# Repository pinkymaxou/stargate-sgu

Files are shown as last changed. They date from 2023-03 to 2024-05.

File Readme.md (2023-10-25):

**Warning**: This project contains several hundred parts to print and hundreds hours of print.
If you decide to take this path you will suffer a lot, you may lose some compatriot in the battle.
You will no longer be the same after that, it could also cause hair loss.

# Stargate Universe

This project is basically a small stargate made to decorate your desk. It features lightning for symbols like in the serie and the ring spins.

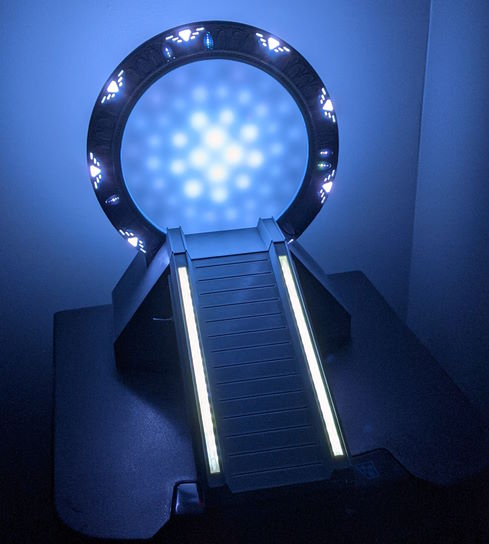
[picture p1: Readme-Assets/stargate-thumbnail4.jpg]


https://www.youtube.com/watch?v=xp08K564FYA for more details.

Unfortunately this project went through a lot of trial and error, so there are more parts than it should have especially in the base.
Optimize it would require making a second gate to test new optimization.
I'm no willing to do that now.

Inspired partly by:

| URL |
|---|
| https://thestargateproject.com/build-a-stargate-and-dhd-3d-printed/ |
| https://www.youtube.com/watch?v=m0cj_5DWYjw&ab_channel=StargateFan |

# Knowns issues

- The start-up and recharge plunger is not perfect, using pogo pin and gold plated female contactor may improve it.

# Copyrights & Thanks

Copyright:
|File | Info
|---|---
| stargateuniverse.woff | Created by : Gilles Nuytens (http://www.thescifiworld.net/fonts.htm)
| eurostile_extended2_bold.woff | https://fontsgeek.com/fonts/eurostile-extended-2-bold?ref=readme
| ancient_virtual.ttf.woff | Created by VirtualCLD (http://www.thescifiworld.net/fonts.htm)
| MGM (for the franchise)
| Explanation and inspiration for the design | https://stargate.fandom.com/wiki/Glyph#Milky_Way_glyphs
| Adafruit | OLED library |

|File | Info
|---|---
| DF Robot | https://www.dfrobot.com/
| Embedded file generator (python) | Created by ducalex https://github.com/ducalex

# Original gate

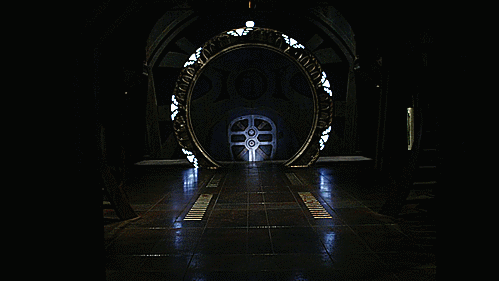
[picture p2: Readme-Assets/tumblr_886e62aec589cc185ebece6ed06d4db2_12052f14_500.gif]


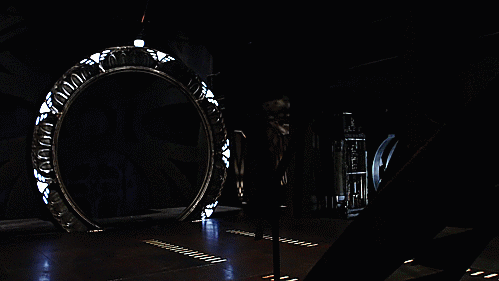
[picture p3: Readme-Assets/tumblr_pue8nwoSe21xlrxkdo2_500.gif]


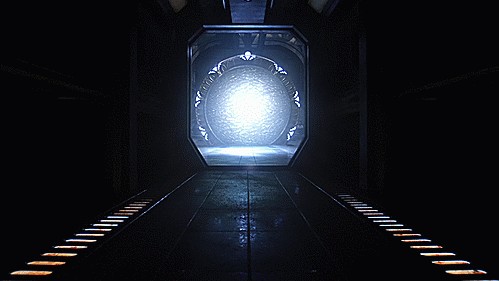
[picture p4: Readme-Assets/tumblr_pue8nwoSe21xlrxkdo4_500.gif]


# Prerequisites

 - Correct knowledge of ESP32 and programming with ESP-IDF
 - At least 22 x 22 cm printer, capable of printing with 0.2 mm nozzle (yes, 0.2mm !)<br>
    **Warning: Don't even think of printing it using a bigger nozzle, it just won't work.**
 - Have some knowledge in electronic.
 - ESP-IDF toolkit installed (tested on IDF 5.0)

# Included softwares

| Name | Description |
|---|---|
| base-fw | Base control firmware |
| ring-factory | Basic firmware to upload firmware into ring |
| ring-fw | Ring firmware |
| tools/otauploader.py | Do upload using HTTP for OTA |
| tools/embeddedgen.py | Generate embedded resources |

# Electronic board

A new electronic board has been created. Not yet tested entierely.

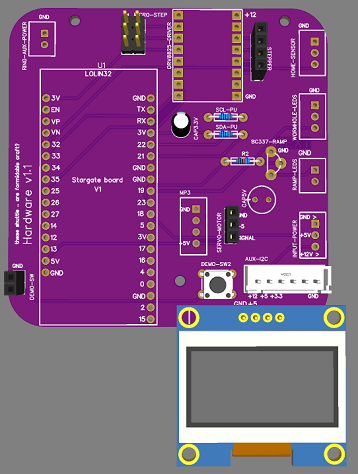
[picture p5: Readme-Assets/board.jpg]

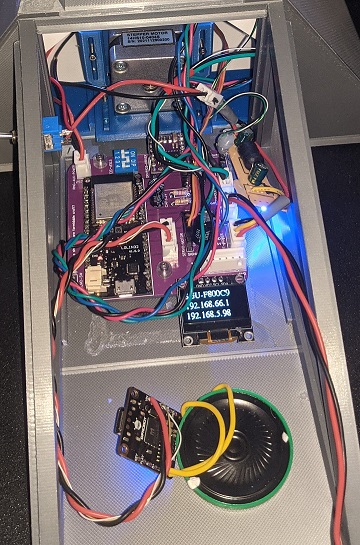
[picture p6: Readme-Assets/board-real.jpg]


# Parts to print

##  Ring

| File name | Count |
|---|---|
| Alignment-block-0.2mm_x9.stl | 9
| Chevron-insert-tool.stl | 1
| Home-magnet-holder_0.4mm-x1.stl | 1
| Inner-ring-0.4mm_x1.stl | 1
| Inner-ring-sensor-holder_0.4mm-x1.stl | 1
| Light-chevron-0.2mm_x18.stl | 18
| Light-chevron-cover-0.2mm-x9.stl | 9
| Magnet-ring-0.2mm-x1.stl | 1
| Module-With_wheel-0.2mm_x18.stl | 18
| Stargate-Back-0.2mm_x1.stl | 1
| Stargate-Back-Transparent-PwrSw_0.2mm-x1 | 1
| Stargate-Back-Transparent-ResetBtn_0.2mm-x1 | 1
| Stargate-Back-TransWindow-0.2mm-x10-12.stl | 12
| Stargate-Front-0.2mm_x1.stl | 1
| Symbols/symbol-template10_0.2mm-x1.stl | 1
| Symbols/symbol-template11_0.2mm-x1.stl | 1
| Symbols/symbol-template12_0.2mm-x1.stl | 1
| Symbols/symbol-template13_0.2mm-x1.stl | 1
| Symbols/symbol-template14_0.2mm-x1.stl | 1
| Symbols/symbol-template15_0.2mm-x1.stl | 1
| Symbols/symbol-template16_0.2mm-x1.stl | 1
| Symbols/symbol-template17_0.2mm-x1.stl | 1
| Symbols/symbol-template18_0.2mm-x1.stl | 1
| Symbols/symbol-template19_0.2mm-x1.stl | 1
| Symbols/symbol-template1_0.2mm-x1.stl | 1
| Symbols/symbol-template20_0.2mm-x1.stl | 1
| Symbols/symbol-template21_0.2mm-x1.stl | 1
| Symbols/symbol-template22_0.2mm-x1.stl | 1
| Symbols/symbol-template23_0.2mm-x1.stl | 1
| Symbols/symbol-template24_0.2mm-x1.stl | 1
| Symbols/symbol-template25_0.2mm-x1.stl | 1
| Symbols/symbol-template26_0.2mm-x1.stl | 1
| Symbols/symbol-template27_0.2mm-x1.stl | 1
| Symbols/symbol-template28_0.2mm-x1.stl | 1
| Symbols/symbol-template29_0.2mm-x1.stl | 1
| Symbols/symbol-template2_0.2mm-x1.stl | 1
| Symbols/symbol-template30_0.2mm-x1.stl | 1
| Symbols/symbol-template31_0.2mm-x1.stl | 1
| Symbols/symbol-template32_0.2mm-x1.stl | 1
| Symbols/symbol-template33_0.2mm-x1.stl | 1
| Symbols/symbol-template34_0.2mm-x1.stl | 1
| Symbols/symbol-template35_0.2mm-x1.stl | 1
| Symbols/symbol-template36_0.2mm-x1.stl | 1
| Symbols/symbol-template3_0.2mm-x1.stl | 1
| Symbols/symbol-template4_0.2mm-x1.stl | 1
| Symbols/symbol-template5_0.2mm-x1.stl | 1
| Symbols/symbol-template6_0.2mm-x1.stl | 1
| Symbols/symbol-template7_0.2mm-x1.stl | 1
| Symbols/symbol-template8_0.2mm-x1.stl | 1
| Symbols/symbol-template9_0.2mm-x1.stl | 1
| symbol-light-guide_0.2mm-x36.stl | 36
| Lower-bridge-0.4mm-x1.stl | 1
| TOTAL | 148

## Base

| File name | Count |
|---|---|
| Back-plunger-anchor_4mm-x2.stl | 2
| Back-plunger-arm_4mm-x1.stl | 1
| Back-plunger-bar_4mm-x1.stl | 1
| Back-plunger-Higher-spring_4mm-x1.stl | 1
| Back-plunger-Lower-spring_4mm-x1.stl | 1
| black-plunger-hammer-cover_4mm-x1.stl | 1
| black-plunger-hammer_4mm-x1.stl | 1
| Board-holder_4mm-x1.stl | 1
| Bottom-plate-v2_4mm-x1.stl | 1
| magnet-gear_4mm-x1.stl | 1
| Mechanic-Anchor-L_4mm-x1.stl |1
| Mechanic-Anchor-R_4mm-x1.stl | 1
| Mechanic-Archor-p2-L_4mm-x1.stl | 1
| Mechanic-Archor-p2-R_4mm-x1.stl | 1
| Outer-back-cover-plug-blocking_4mm-x1.stl | 1
| Outer-back-cover-plug_4mm-x1.stl | 1
| Outer-back-cover_4mm-x1.stl | 1
| Outer-back-plate-reinforcement_4mm-x1.stl | 1
| Outer-back-plate_4mm-x1.stl | 1
| Outer-bottom-plate2_4mm-x1.stl | 1
| Outer-bottom-plate_4mm-x1.stl | 1
| Outer-front-plate_4mm-x1.stl | 1
| Outer-side-plate#1_4mm-x1.stl | 1
| Outer-side-plate#2_4mm-x1.stl | 1
| ramp-light-guide_4mm-x2.stl | 2
| Ramp_4mm-x1.stl | 1
| Side-back-cover-L_4mm-x1.stl | 1
| Side-back-cover-R_4mm-x1.stl | 1
| Side-ramp-cover-L_4mm-x1.stl | 1
| Side-ramp-cover-R_4mm-x1.stl | 1
| spacer_4mm-x4.stl | 4
| Stepper-bracket_4mm-x1.stl | 1
| Stepper-mount-1_4mm-x1.stl | 1
| Stepper-mount-2_4mm-x1.stl | 1
| top-cover_4mm-x1.stl | 1
| Truss#1_4mm-x1.stl | 1
| Truss#2_4mm-x1.stl | 1
| Side-overcover-L_4mm-x1.stl | 1
| Side-overcover-R_4mm-x1.stl | 1
| TOTAL | 44

## Wormhole

| File name | Count |
|---|---|
| Wormhole.stl | 1
| Wormhole-outer-rim.stl | 1
| Wormhole-filter.stl | 1
| TOTAL | 3

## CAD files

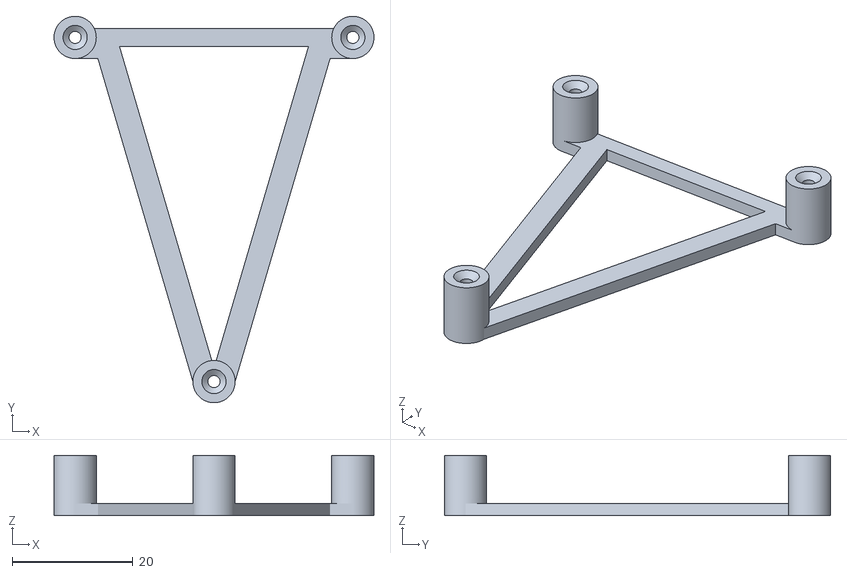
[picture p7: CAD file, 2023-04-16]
Build-Instructions/Base/Board-holder_4mm-x1.stl
53.0 x 64.0 x 10.0

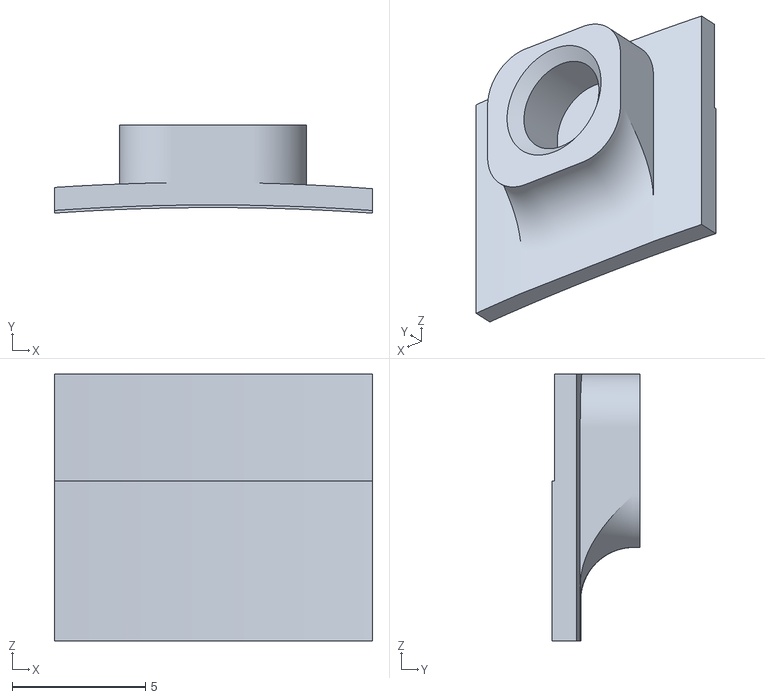
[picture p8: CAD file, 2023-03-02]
Build-Instructions/Ring/Home-magnet-holder_0.4mm-x1.stl
11.9 x 3.32 x 10.0

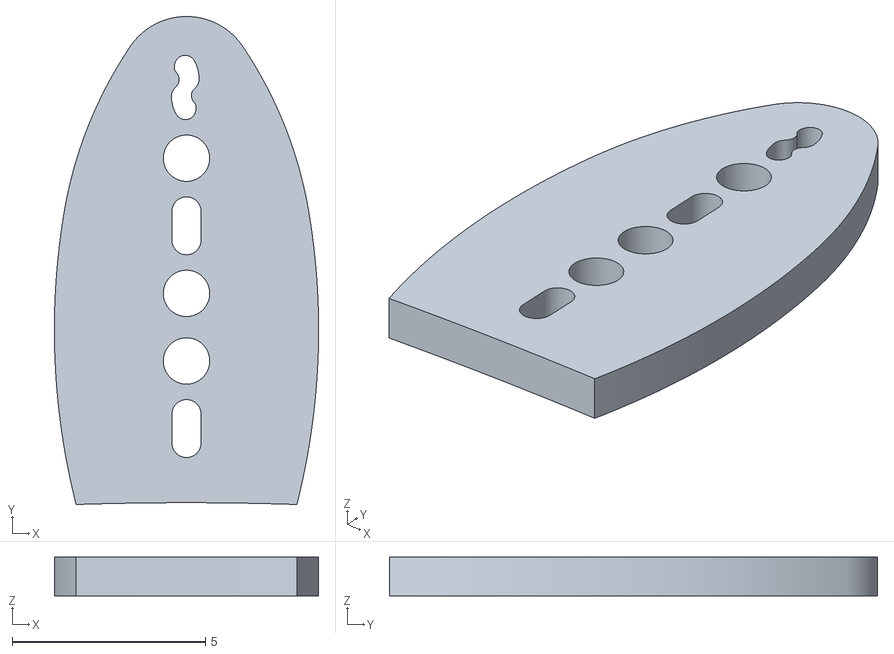
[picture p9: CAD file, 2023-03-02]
Build-Instructions/Ring/Symbols/symbol-template1_0.2mm-x1.stl
6.84 x 12.6 x 1.00

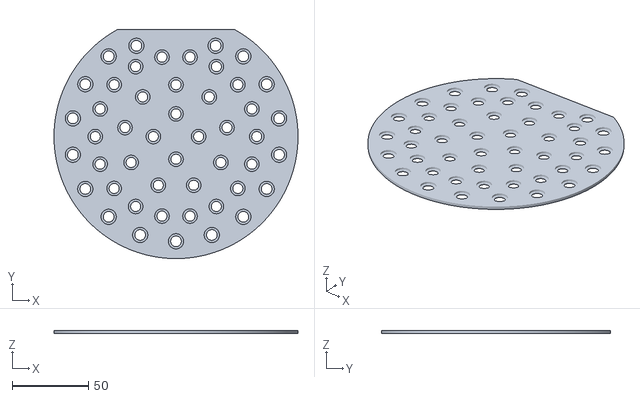
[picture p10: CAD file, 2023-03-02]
Build-Instructions/Wormhole/Wormhole.stl
160.2 x 150.4 x 2.00

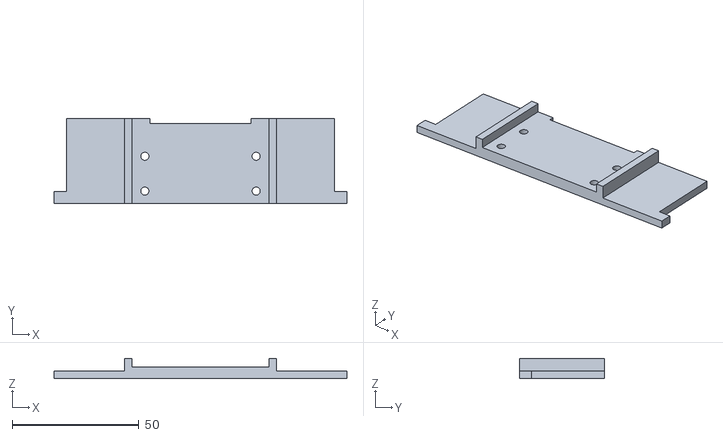
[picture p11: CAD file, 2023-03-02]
Build-Instructions/Base/Stepper-mount-1_4mm-x1.stl
115.8 x 33.8 x 8.00

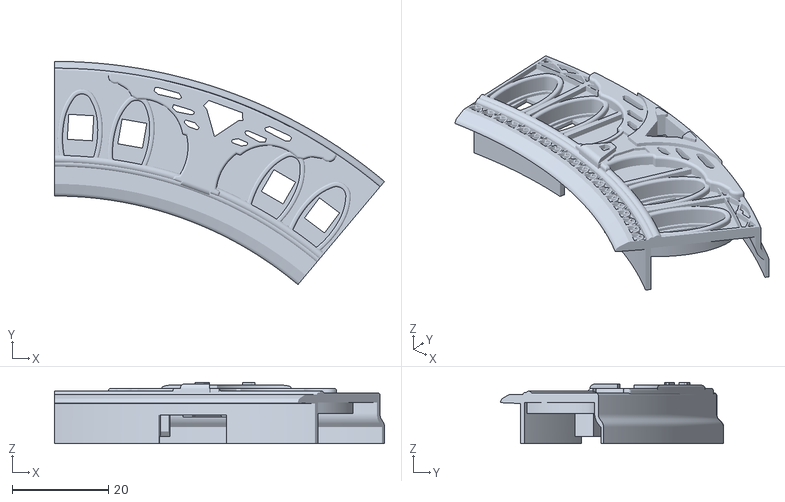
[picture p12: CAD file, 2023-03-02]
Build-Instructions/Ring/TestPart-Stargate-Front.stl
68.4 x 46.3 x 12.7

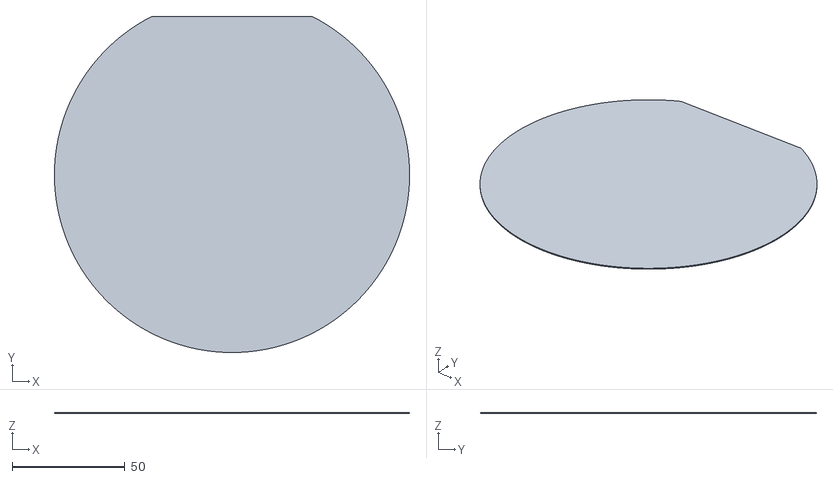
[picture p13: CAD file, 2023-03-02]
Build-Instructions/Wormhole/Wormhole-filter.stl
157.5 x 149.0 x 0.5

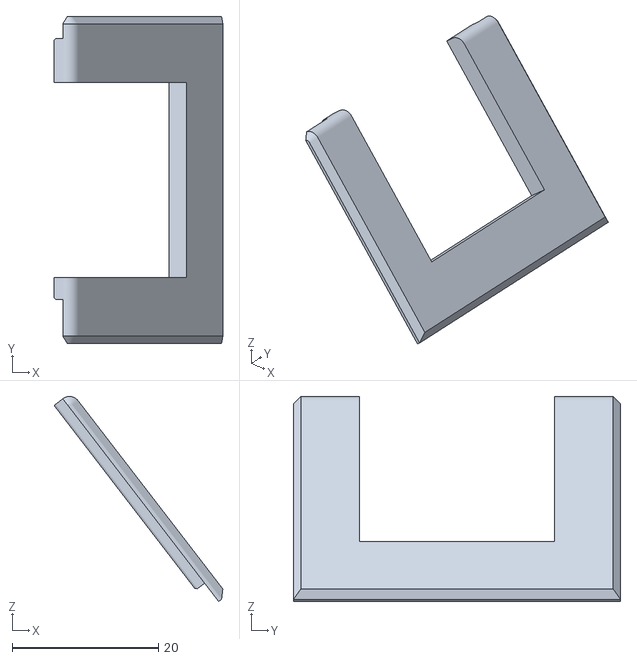
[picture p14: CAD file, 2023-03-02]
Build-Instructions/Base/Side-overcover-R_4mm-x1.stl
23.1 x 44.7 x 28.0

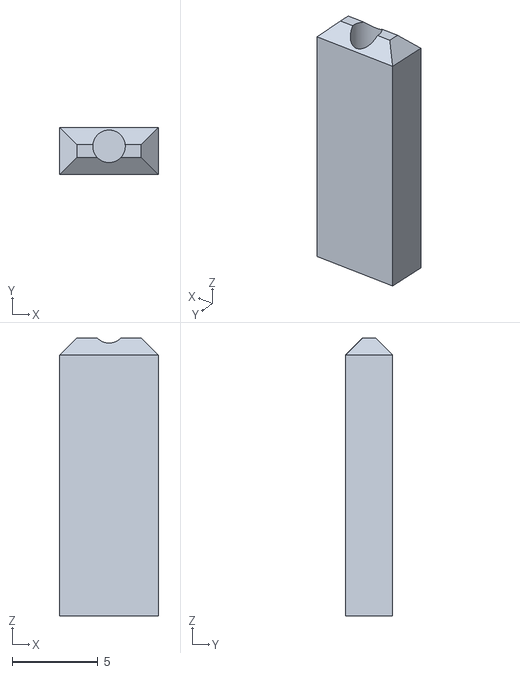
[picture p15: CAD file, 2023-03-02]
Build-Instructions/Ring/Alignment-block-0.2mm_x9.stl
5.76 x 2.76 x 16.2

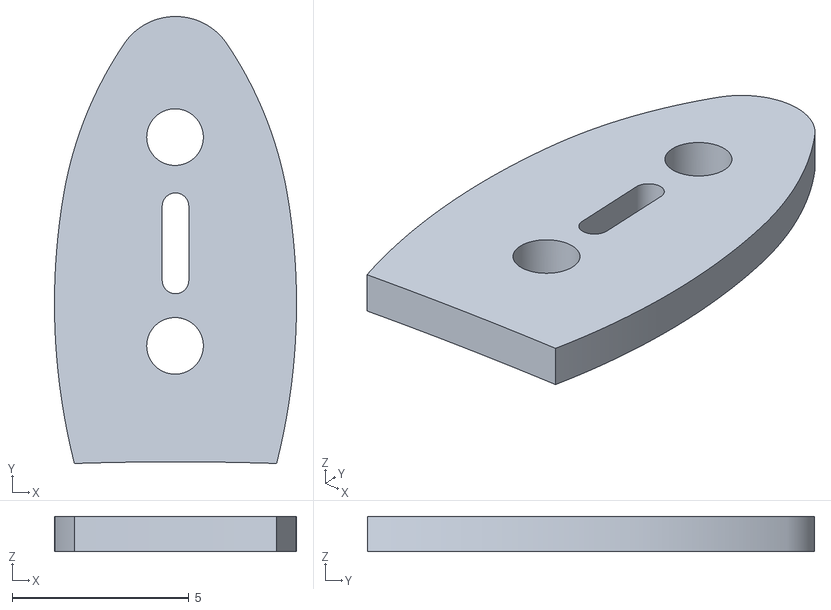
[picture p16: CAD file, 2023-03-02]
Build-Instructions/Ring/Symbols/symbol-template34_0.2mm-x1.stl
6.84 x 12.6 x 1.00

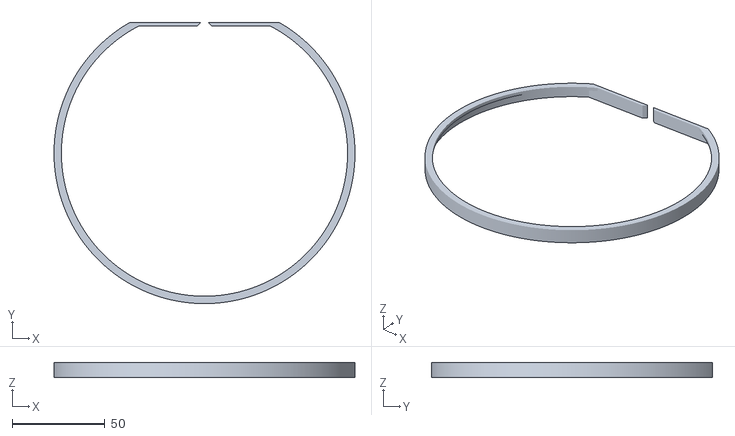
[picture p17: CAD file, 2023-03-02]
Build-Instructions/Wormhole/Wormhole-outer-rim.stl
162.0 x 151.3 x 8.00

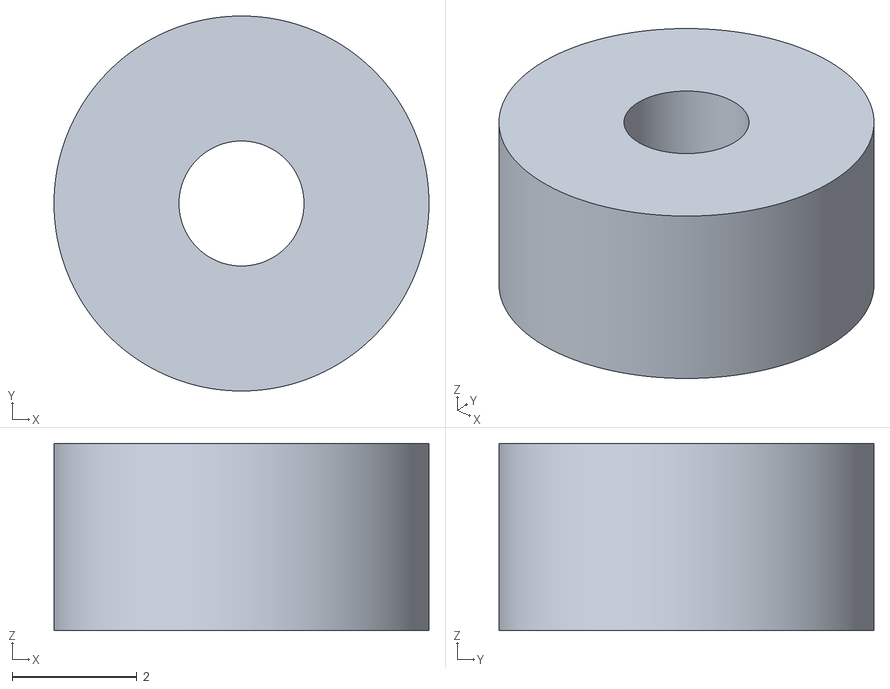
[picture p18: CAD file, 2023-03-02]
Build-Instructions/Base/spacer_4mm-x4.stl
6.00 x 6.00 x 3.00

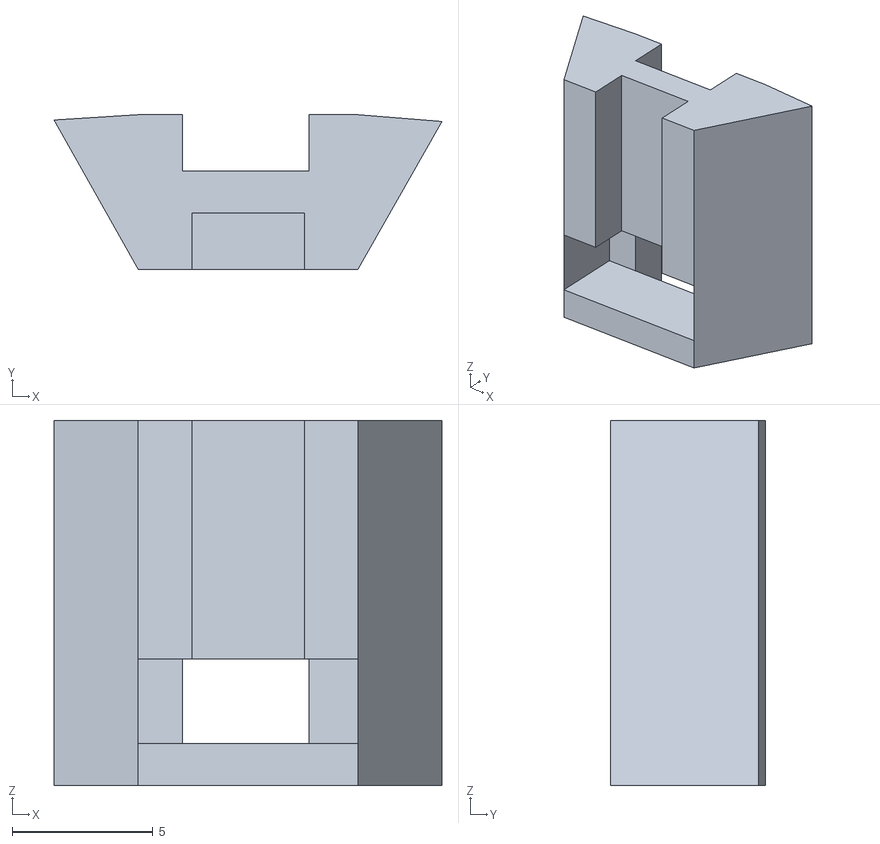
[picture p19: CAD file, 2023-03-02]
Build-Instructions/Ring/Inner-ring-sensor-holder_0.4mm-x1.stl
13.8 x 5.50 x 13.0

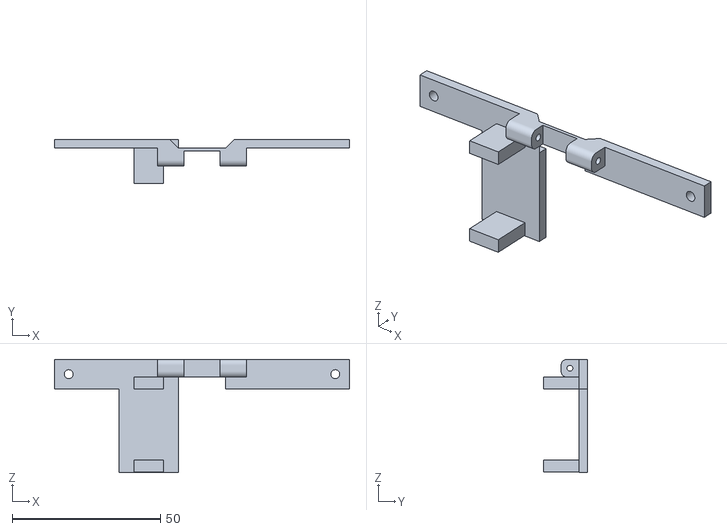
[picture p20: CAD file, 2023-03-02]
Build-Instructions/Base/Back-plunger-bar_4mm-x1.stl
99.6 x 15.0 x 38.3

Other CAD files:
Build-Instructions/Ring/Symbols/symbol-template18_0.2mm-x1.stl
Build-Instructions/Ring/Symbols/symbol-template3_0.2mm-x1.stl
Build-Instructions/Ring/Magnet-ring-0.2mm-x1.stl
Build-Instructions/Ring/Symbols/symbol-template16_0.2mm-x1.stl
Build-Instructions/Base/Back-plunger-Higher-spring_4mm-x1.stl
Build-Instructions/Base/Back-plunger-Lower-spring_4mm-x1.stl
Build-Instructions/Base/Back-plunger-anchor_4mm-x2.stl
Build-Instructions/Base/Back-plunger-arm_4mm-x1.stl
Build-Instructions/Base/Bottom-plate-v2_4mm-x1.stl
Build-Instructions/Base/Mechanic-Anchor-L_4mm-x1.stl
Build-Instructions/Base/Mechanic-Anchor-R_4mm-x1.stl
Build-Instructions/Base/Mechanic-Archor-p2-L_4mm-x1.stl
Build-Instructions/Base/Mechanic-Archor-p2-R_4mm-x1.stl
Build-Instructions/Base/Outer-back-cover-plug-blocking_4mm-x1.stl
Build-Instructions/Base/Outer-back-cover-plug_4mm-x1.stl
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

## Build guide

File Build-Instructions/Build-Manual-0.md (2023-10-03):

# Material prerequisite

## Electronics

| Description | Quantity | URL
|---|---|---|
| MOSFET P Channel | 1 | https://www.aliexpress.com/item/32884055864.html |
| NPN Transistor (BC337) | 1 |  |
| LEDs WS2812B | 100 | https://www.aliexpress.com/item/1005002657432751.html |
| 693ZZ bearings (8mm wide, 4mm thick, 3mm inner)  | 9 |  https://www.aliexpress.com/item/557757520.html |
| M5Stack Official M5Stamp Pico | 1 |  https://www.aliexpress.com/item/1005003449579749.html |
| LiPo Charger with 5v boost | | https://www.aliexpress.com/item/4000935870120.html |
| LiPo battery | 4x 100mA  | https://www.aliexpress.com/item/32853990764.html (any will do as long as it fit into the ring) |
| ESP32, example: Lolin32 | 1 | Any with enough output pin will do. |
| Fermion DFPlayer Pro Mini MP3 | 1 | https://www.aliexpress.com/item/4000394488862.html |
| DRV8825 Stepper Motor Controller | 1 | https://www.amazon.ca/-/fr/DRV8825-remplacement-TMC2208-Dissipateur-thermique/dp/B095LRJR2S |
| Resistors kit | |
| Capacitor kit | |
| A few schottky diodes | |
| All kind of wires | (24 to 26 AWG mostly) |
| 12 volts to 5 volts step converter (2A) | 1 | https://www.aliexpress.com/item/1005001534795169.html
| 12 mm tactile switch | 1 |
| Hall-Effect Sensor Digital 3144 | 1 | https://www.aliexpress.com/item/32823025060.html (Any will do as long as it's digital)
| JST Connecteur Kit 2.54 mm | 1 | https://www.amazon.ca/Bestgle-Connector-JST-XHP-Housing-Adapter/dp/B07MBCLPBK/ref=asc_df_B07MBCLPBK/

## Mechnical parts

| Description | Quantity | URL |Comments
|---|---|---|---|
| NEMA 14 stepper | 1 | https://www.amazon.ca/0-9deg-steps-Precision-Stepper-15-6oz/dp/B00PNEPZQC
| 4x2 mm magnets  | 160 | https://www.aliexpress.com/item/1005002591601630.html |
| Privacy film  | 25x25 cm at least | https://www.aliexpress.com/item/32967449727.html |
| Copper tape  | 1 | https://www.aliexpress.com/item/1005002822966859.html |
| Plexiglass 20x20cm (recommend buying spare)  | 1 + 1 spare | https://www.aliexpress.com/item/32833660352.html |
| Servo 9g | 1 | https://www.amazon.ca/-/fr/Servo-num%C3%A9rique-Micro-Metal-mod%C3%A8le/dp/B07FPJYM5T | We tried cheap one but they proved to be problematic, one died suddently and the other draw too much current sometime. You may have to invest in something better.
| M2 screws kit | 1 | https://www.amazon.ca/-/fr/Hilitchi-Assortiment-hexagonale-acier-inoxydable/dp/B014ONS02S | You needs several lengths
| M3 screws kit | 1 | https://www.amazon.ca/Assortiment-cruciformes-cylindrique-acier-inoxydable/dp/B075RCVVYN/ | You needs several lengths

## 3D Printing parts

| Description | Quantity | URL
|---|---|---|
| Nozzle 0.2mm | 1 | Required to get nice results

## Recommendations

Parts are printed at very high resolution (by FDM standard) and printing require for several days in some case. It's very important to have a good way to ensure it sticks in place.

| Description | Quantity | URL
|---|---|---|
| Dremel Purple Glue | 1 | https://www.amazon.ca/Dremel-GS45-01-Glue-Sticks/dp/B077FVQ3DX
| Magigoo | 1 | https://shop3d.ca/products/magigoo-3d-printing-adhesive-50ml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

## MISC

| Description | Quantity | Description
|---|---|---|
| Gorilla Super Glue | 1 | Used to glue the most important parts.
| Canopy Glue | 1 | Need a glue that turn transparent. Gorilla glue stain the plexiglass and leave horrible traces.
| Hot Glue | 1 | It could be done with canopy glue too but it's easier to remove hot glue if necessary.
| Small clamps to hold parts while curing | 1 |

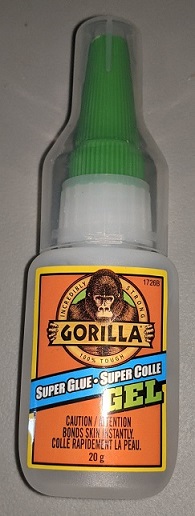
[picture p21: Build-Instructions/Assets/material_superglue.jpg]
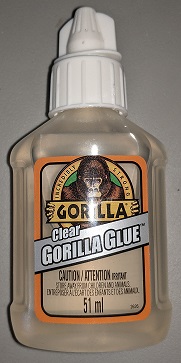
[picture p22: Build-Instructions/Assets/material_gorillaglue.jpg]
  

## Required plastics

Basically color is up to you, but you will probably needs at least 3 colors.<br>
Nothing prevent you from painting parts if you can't find the right plastic color. If you do it, we suggest using dark PLA before painting over the ring, to be sure lights do not leak.

| Color | Used for | Comments
|---|---|---|
| Dark gray or black PLA | Ring | The ring in the serie is almost black if not black. The one we made was gray but not dark enough, if we could do it again we would likely make it black |
| Transparent PLA | Ring | Used for chevron illumination and light diffusion. It may be possible to use white instead but we suggest you to test it before commiting yourself.
| White PLA | Ring/Base | Used for reflectors but can be used for any parts that is not visible. (example, bearing module, inner ring, alignment block etc ...)
| Sand PLA | Base | Sand like color, yes we realise there are many possible color for sand so let's say the same color as pyramid of egypt?

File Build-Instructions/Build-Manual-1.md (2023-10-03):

# Recommendation

## Before printing

We provide "TestPart-Stargate-Front.stl" part to test printing 1/9 of the front stargate part.<br>
It allows you to test material or print settings before doing the big part.

We recommend you to print these parts using the color or plastic of your choice :

- TestPart-Stargate-Front.stl
- Light-chevron-0.2mm_x18.stl
- symbol-light-guide_0.2mm-x36.stl
- symbol-template1_0.2mm-x1.stl

It is better if you also have one WS2812B to test the chevron and symbol lightning.<br>
The LED shouldn't be at full power to test symbols, only 5/255 PWM is enough to see it clearly.<br>
It could be higher for chevron but your don't gain anything going beyond 160/255 except excessive power loss.<br>

If you want to use a resin printer for symbols you can, but you will likely have to paint them because resin transparency is not adequate in our experience.

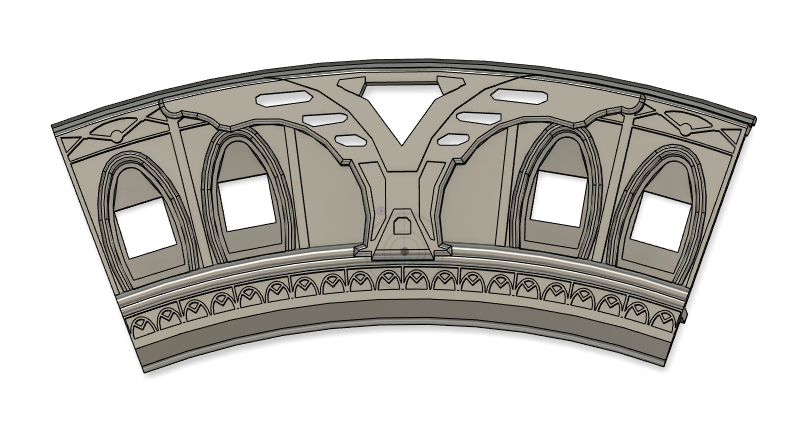
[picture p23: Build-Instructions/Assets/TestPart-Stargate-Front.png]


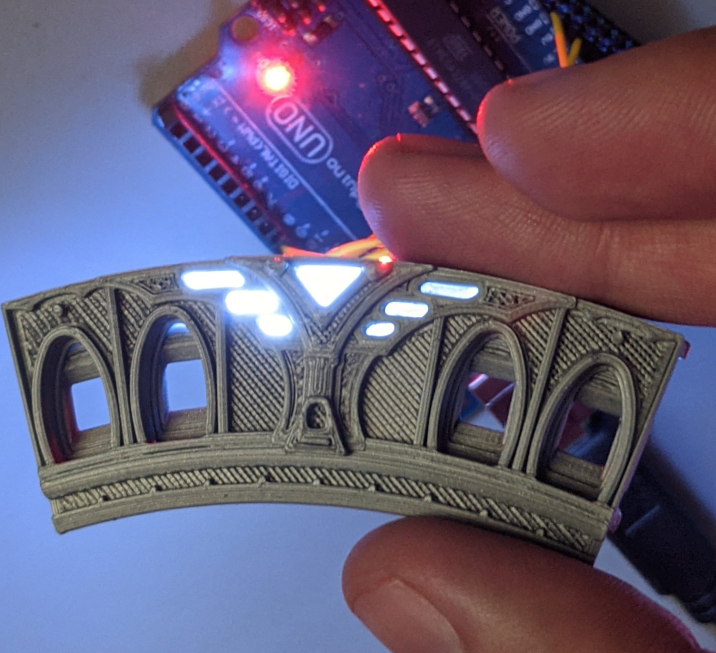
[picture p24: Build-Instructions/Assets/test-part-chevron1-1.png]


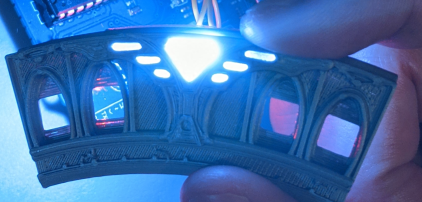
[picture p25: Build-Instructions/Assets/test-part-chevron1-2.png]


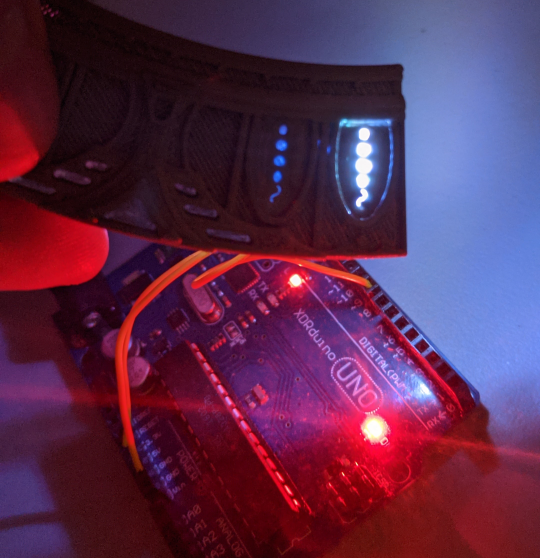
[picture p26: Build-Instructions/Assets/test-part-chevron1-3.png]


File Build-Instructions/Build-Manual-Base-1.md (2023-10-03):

# Base assembly

Don't worry about the ringmotor assembly, it could be inserted later.<br>
It is designed to be easy to disassemble.

 - You need a lot of small clamp if you want to do a decent job. we have found them at dollar store and they worth every penny.
 - Gorilla glue or canopy glue

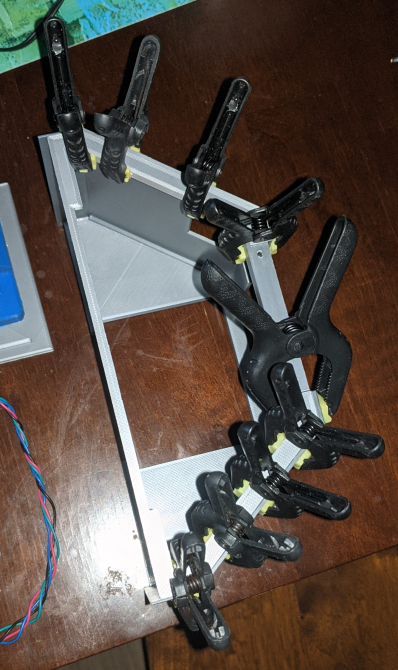
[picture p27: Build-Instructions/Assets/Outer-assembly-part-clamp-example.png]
 

## Glue base parts #1

Glue all those parts together, use the picture to guide you.<br>
You needs those part to continue:

 - Outer-bottom-plate_4mm-x1.stl
 - Outer-bottom-plate2_4mm-x1.stl
 - Outer-front-plate_4mm-x1.stl
 - Outer-side-plate#1_4mm-x1.stl
 - Outer-side-plate#2_4mm-x1.stl

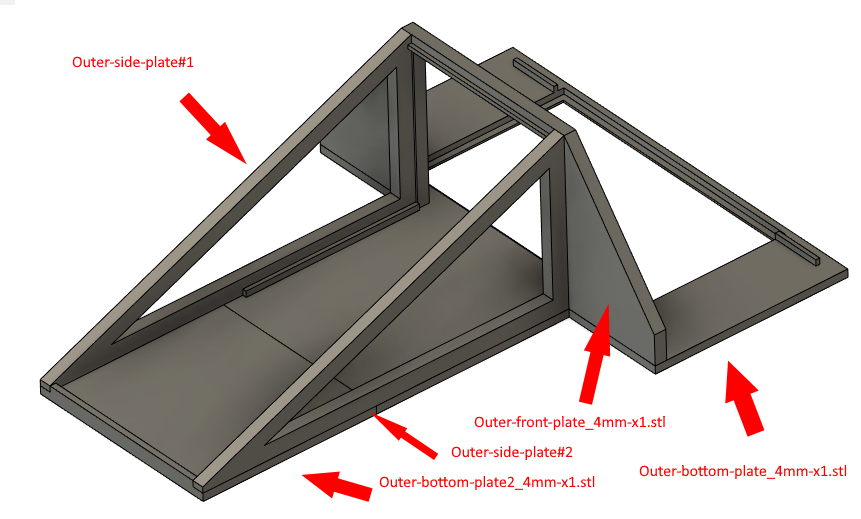
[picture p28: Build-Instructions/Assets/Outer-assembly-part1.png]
 

## Glue base parts #2

Glue Outer-back-plate_4mm-x1.stl to the existing base part #1.

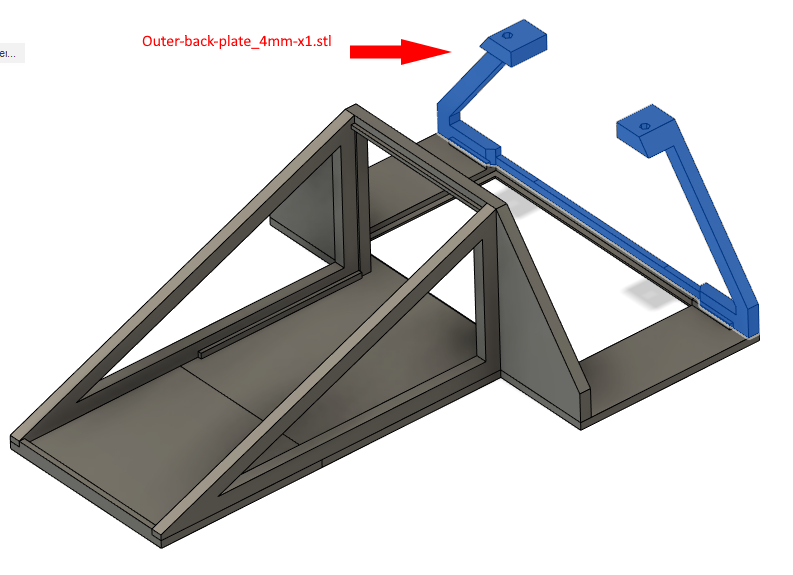
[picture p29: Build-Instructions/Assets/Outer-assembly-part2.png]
 

## Glue base parts #3

You needs to ensure "Bottom-plate-v2_4mm-x1.stl" is in place, IT SHOULDN'T BE GLUED! The part is designed to be removable. It's only there to use as a guide when "Mechanic-Anchor-L_4mm-x1.stl" and "Mechanic-Anchor-R_4mm-x1.stl" get glued.

Ensure to not accidentally glue anything else, don't put too much glue.<br>
Use clamps to hold these parts in place.

To be glued to "Outer-bottom-plate_4mm-x1.stl"
- Mechanic-Anchor-L_4mm-x1.stl
- Mechanic-Anchor-R_4mm-x1.stl

These parts should be in place, but NOT GLUED, only as a guide:
- Mechanic-Archor-p2-L_4mm-x1.stl
- Mechanic-Archor-p2-R_4mm-x1.stl

Once everything is cured, you can remove "Mechanic-Archor-p2-L_4mm-x1.stl" and "Mechanic-Archor-p2-R_4mm-x1.stl" by sliding them.

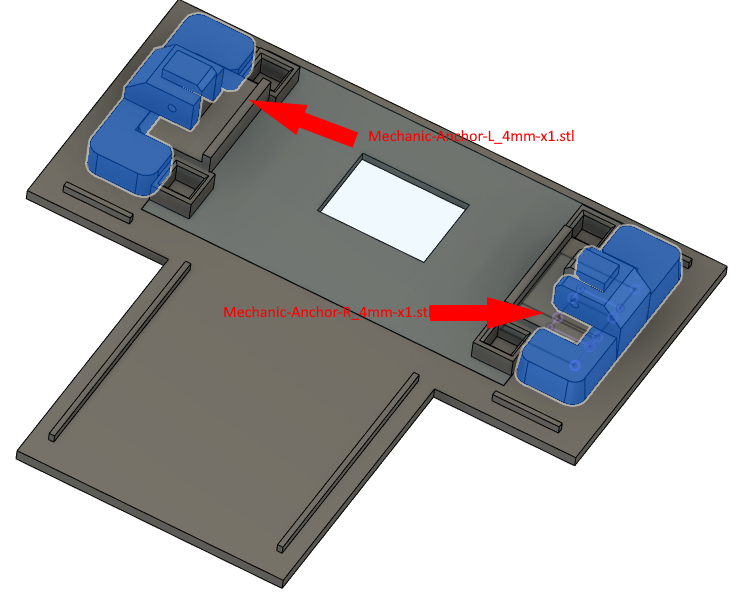
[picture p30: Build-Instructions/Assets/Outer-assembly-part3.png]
 

It should looks like this once once you remove "Mechanic-Archor-p2-L_4mm-x1.stl", "Mechanic-Archor-p2-R_4mm-x1.stl" and "Bottom-plate-v2_4mm-x1.stl".

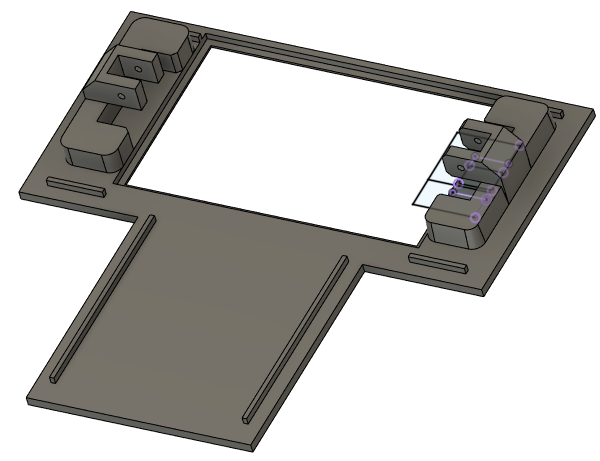
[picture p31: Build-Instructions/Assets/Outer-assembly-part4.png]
 

## Install M2 screws

You need two M2 nuts and a soldering iron or a ligher.<br>
You need to push heated M2 nuts into their designated holes. Be careful to not overheat.

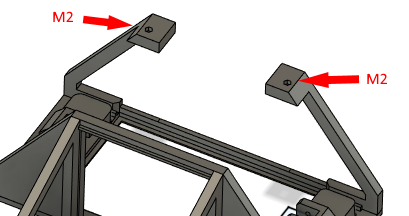
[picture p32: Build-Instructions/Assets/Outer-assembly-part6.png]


## Glue base parts #4

Glue side covers, you needs to use clamp and maybe tape. You can use painter tape where clamps are not a good option.

- Side-back-cover-L_4mm-x1.stl
- Side-back-cover-R_4mm-x1.stl
- Side-overcover-L_4mm-x1.stl
- Side-overcover-R_4mm-x1.stl

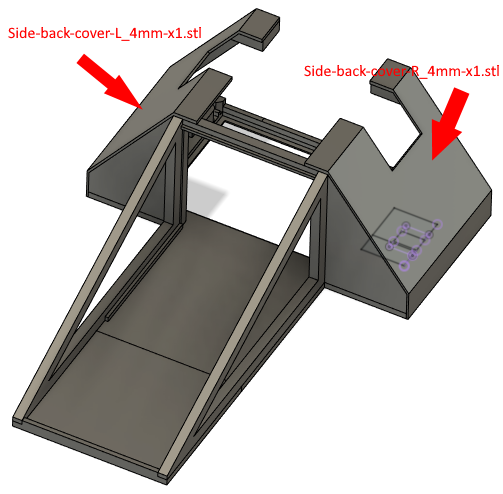
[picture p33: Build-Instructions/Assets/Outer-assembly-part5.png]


Overcovers are not mandatory, they correct a mistake we made on the side cover STL.<br>
we could have corrected it but we feared it could introduce more errors.

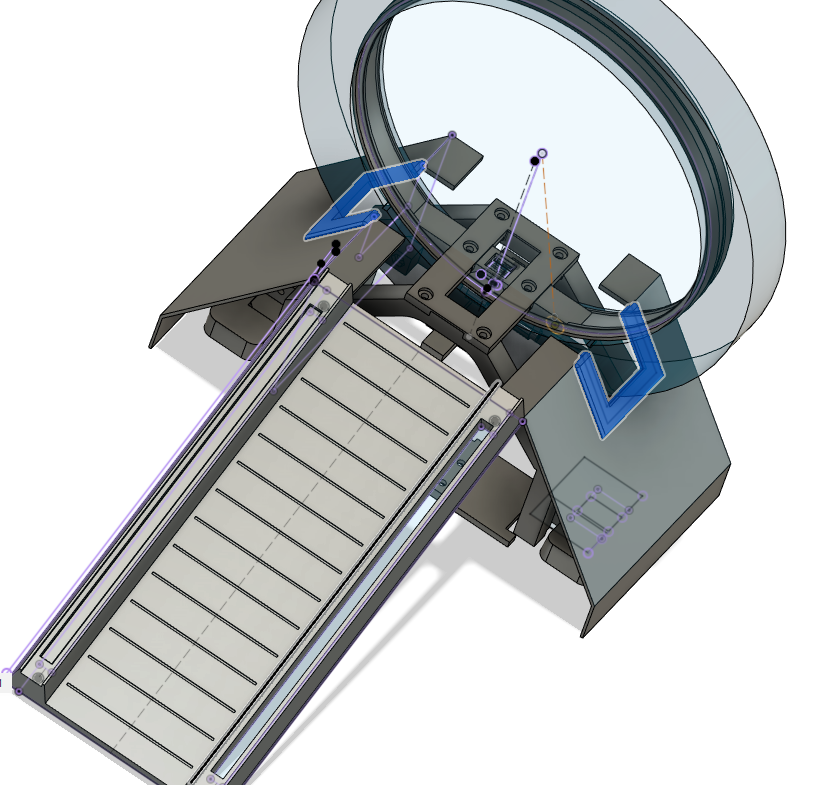
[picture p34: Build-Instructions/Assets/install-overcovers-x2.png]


## Install RingMotor assembly in place

You can install the ring motor assembly if you want.<br>
All you have to do is insert the assembly where it should go then slide these parts:<br>

- Mechanic-Archor-p2-L_4mm-x1.stl
- Mechanic-Archor-p2-R_4mm-x1.stl

You can use an M3x25 screws to secure it in place but friction should be enough.

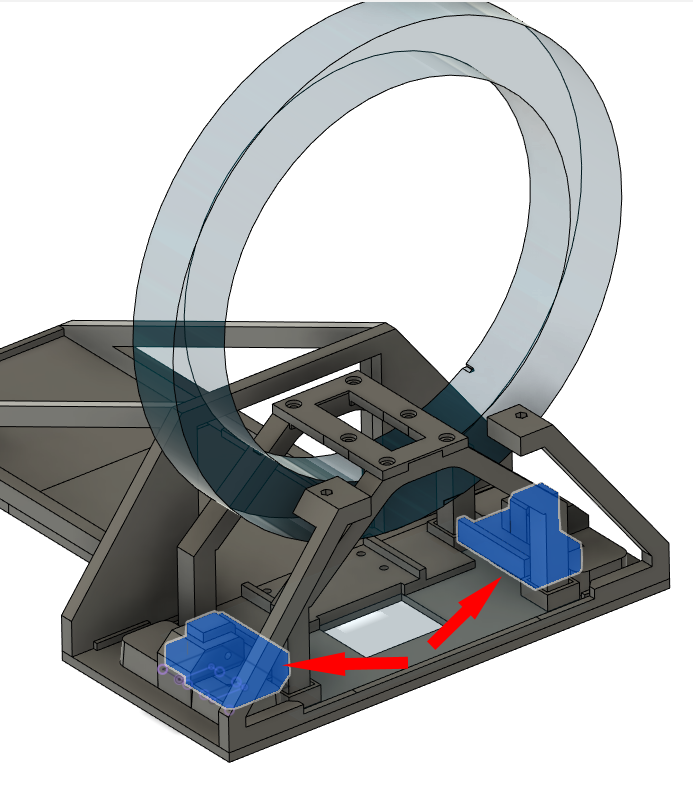
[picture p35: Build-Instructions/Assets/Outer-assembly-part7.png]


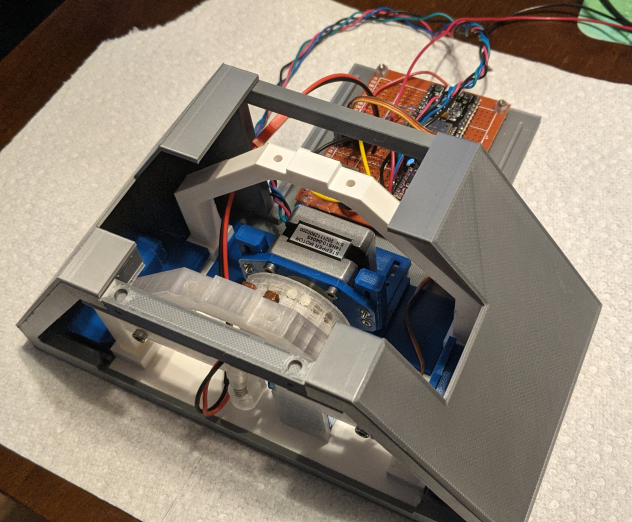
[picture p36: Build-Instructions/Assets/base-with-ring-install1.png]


## Install the reinforcement

You can install "Outer-back-plate-reinforcement_4mm-x1.stl" using two M2x12 screws (not exactly sure about the length).<br>
The base is designed to allow the mecanism to be removed freely.

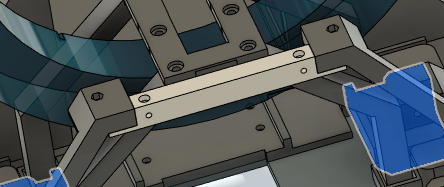
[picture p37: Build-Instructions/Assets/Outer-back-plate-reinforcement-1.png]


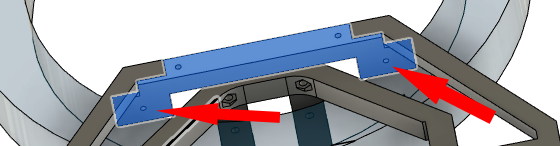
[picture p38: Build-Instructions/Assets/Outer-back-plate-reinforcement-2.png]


## Install back-cover (Outer-back-cover_4mm-x1.stl)

This part is designed to accommodate pretty much any barel jack or connector.<br>
But you have to design it yourself, use "Outer-back-cover-plug_4mm-x1.stl" as a template.<br>
You can glue it to "Outer-back-cover_4mm-x1.stl" using gorilla glue.<br>
The back cover is designed to hold in place using M2x15 screws. It is screwed into plastic because it doesn't needs real structural integrity.

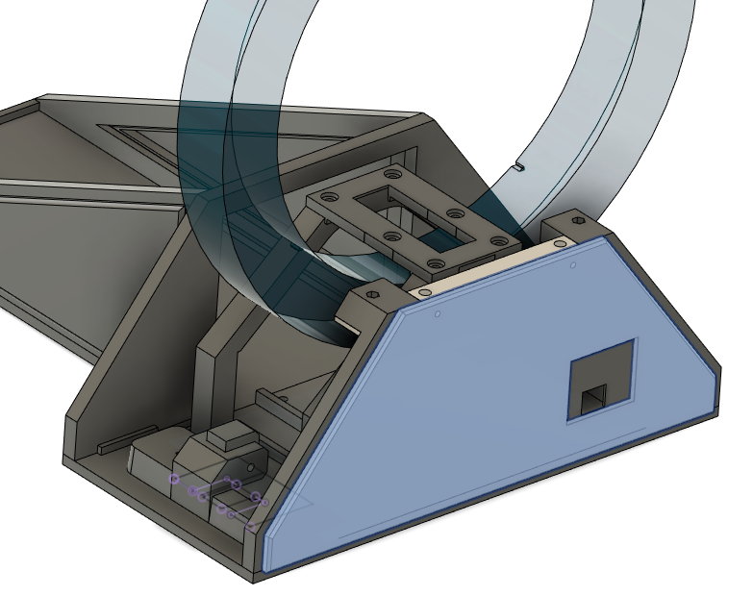
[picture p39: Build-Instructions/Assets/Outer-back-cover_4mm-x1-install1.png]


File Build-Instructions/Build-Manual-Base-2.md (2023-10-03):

# Base assembly #2

## Assemble ramp lights

"ramp-light-guide_4mm-x2.stl" are meant to be printed using transparent PLA.

Insert "ramp-light-guide_4mm-x2.stl" into their locations on "Ramp_4mm-x1.stl", use canopy glue because gorilla glue may have white residues.<br>
The ramp is designed to be removed easily at will. You can add magnets into it if you want, there are holes for it but it's not necessary.

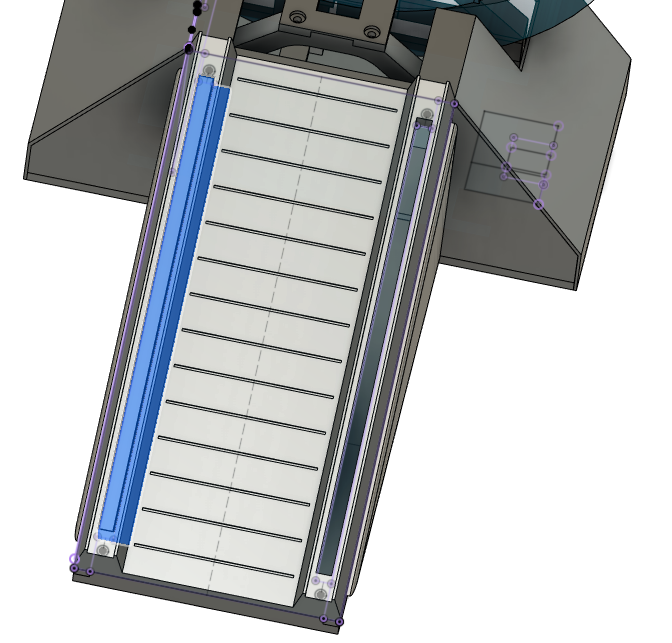
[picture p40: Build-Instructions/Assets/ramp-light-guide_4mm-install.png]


## Install "top-cover_4mm-x1.stl"

Install it on the top, friction alone should be enough to hold it in place but you can glue magnets if you want.

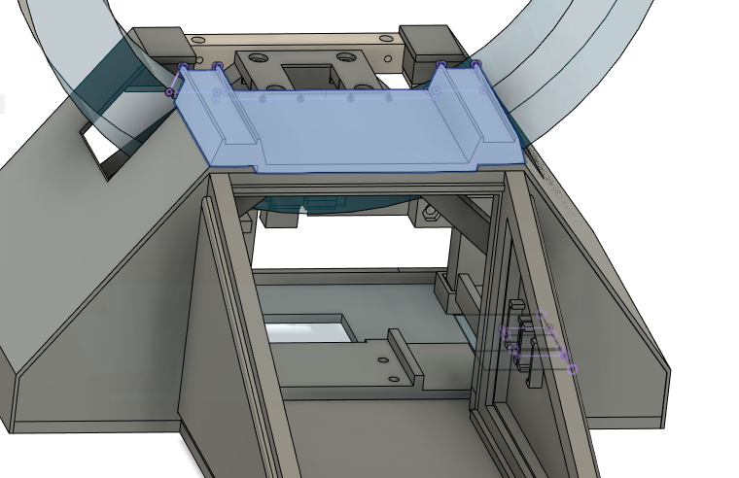
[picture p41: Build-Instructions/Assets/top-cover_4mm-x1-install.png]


## Install side ramp covers

If they hold by themselves just by friction then don't glue them, it's covenient to be able to remove them when working in the electronic zone under the ramp.

- Side-ramp-cover-L_4mm-x1.stl
- Side-ramp-cover-R_4mm-x1.stl

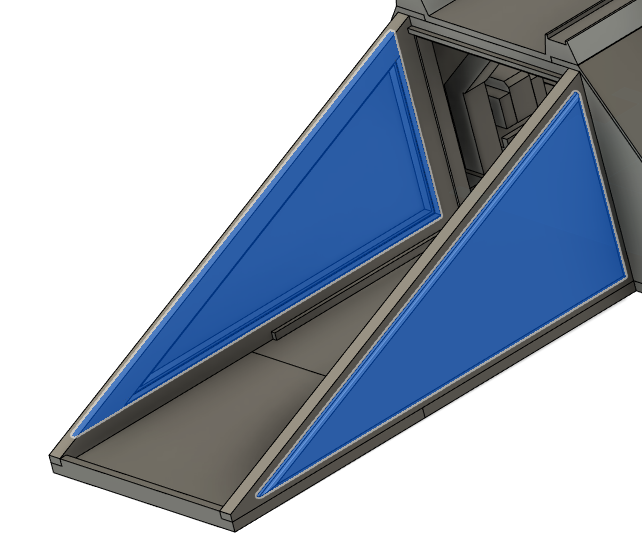
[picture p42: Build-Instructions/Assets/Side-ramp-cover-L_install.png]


## Lamp lightning

- You need to cut a 12 white led strip into two 18 cm strips.
- Wire them in parallel and add a connector to it.
- Glue led strip under "ramp-light-guide_4mm-x2.stl", use clamp to hold them in place during the the curing process.
- Add electrical black tape to prevent light from leaking elsewhere

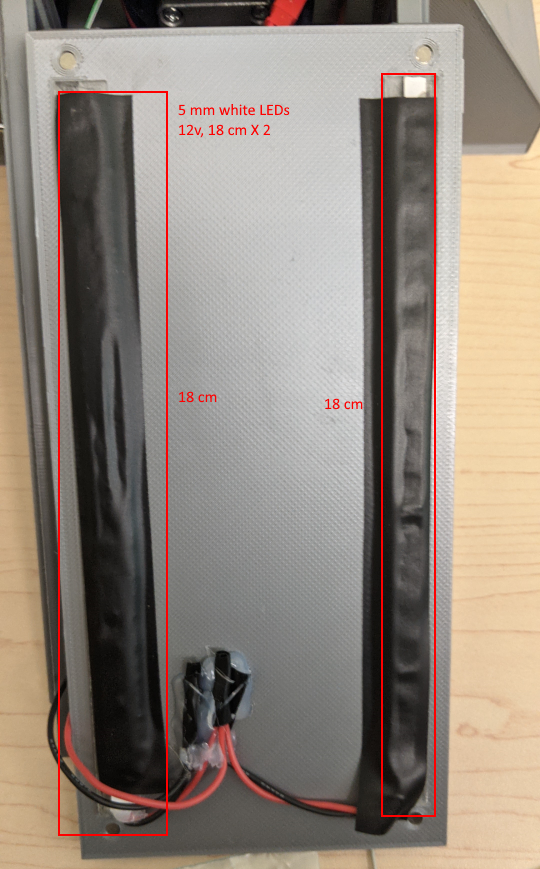
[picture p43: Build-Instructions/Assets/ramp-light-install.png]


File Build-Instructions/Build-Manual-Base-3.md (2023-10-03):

# Base electronic

We use the Lolin32. Former attempt using NodeMCU didn't go well. Likely a bad copy.

 - You can use JST connector or anything else as long as it suit your needs. You can also just solder everything to the board but it's not recommended.

Knowns issues:

 - We used 1A 12v to 5v regulator from dollar store, it proved to be unsufficient in some situation like when the servo motor move or the board starts. So 3A or more should be better.

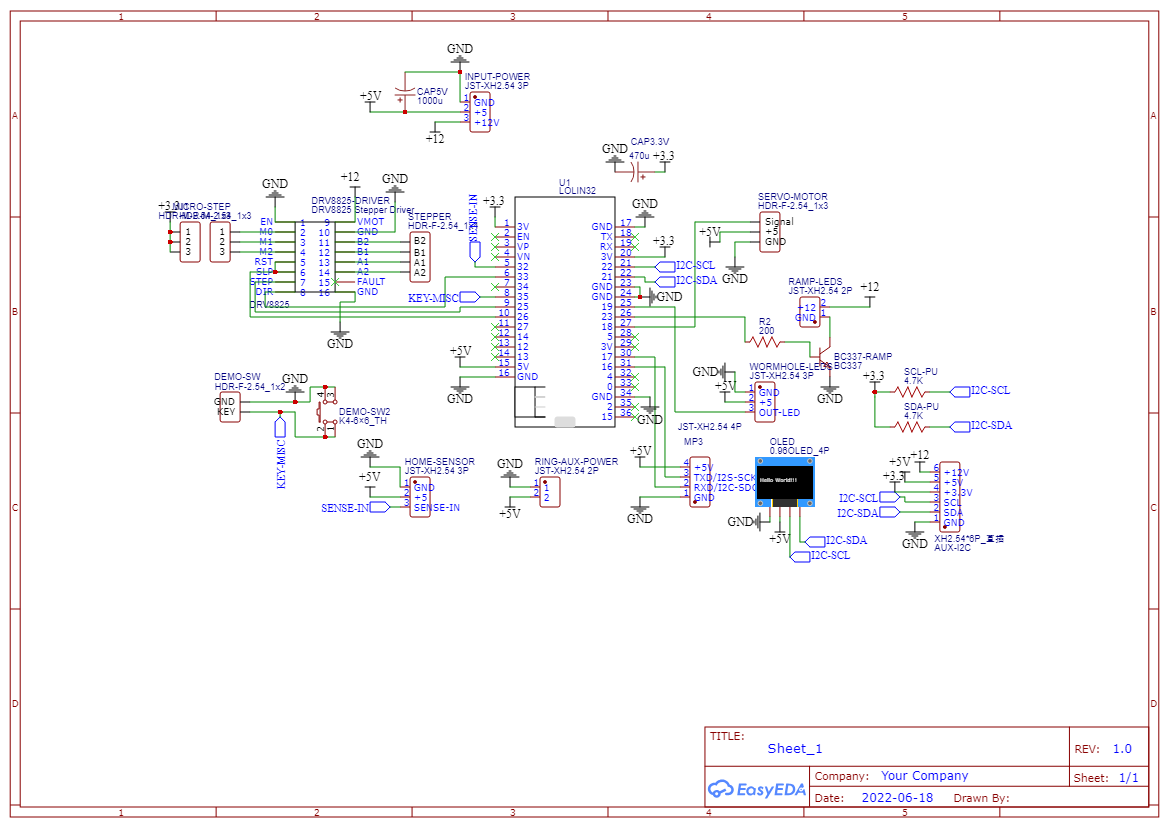
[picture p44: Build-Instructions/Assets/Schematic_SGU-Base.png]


# WS2812B

Based on empirical measurements, there is the average power consumption for WS2812B.<br>
It needs ~1 mA at 0 PWM.

| Channel | Power usage at 255 (mA) |
|---|---|
| RED	 | 13.14084507 |
| GREEN	 | 13.01408451 |
| BLUE	 | 13.16901408 |
| RGB (White) | 35.38 |

## Stepper Driver (DRV8825)

We use a DRV8825 but you can use anything else.
We run in 1/16 steps but it's possible to go higher or lower, but it will require some software changes.
It sounds better at 1/16 but it's perfectly workable at 1/8.

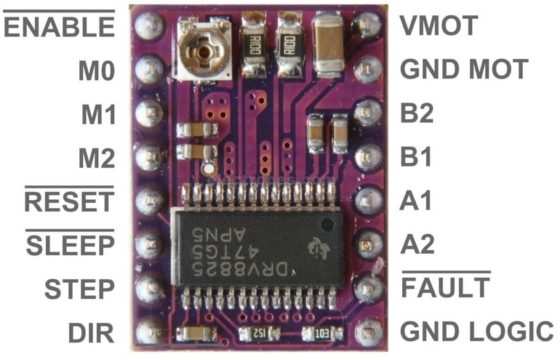
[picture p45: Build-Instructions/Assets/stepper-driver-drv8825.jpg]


| M0 | M1 | M2 | Microstep Resolution
|---|---|---|---:|
| Low | Low | Low | Full step
| High | Low | Low | 1/2 step
| Low | High | Low | 1/4 step
| High | High | Low | 1/8 step
| Low | Low | High | 1/16 step
| High | Low | High | 1/32 step
| Low | High | High | 1/32 step
| High | High | High | 1/32 step

The photo is old, I used JST connector later because the job is prettier.
(No attachement in this photo, perhaps a STL for attach will be made later)

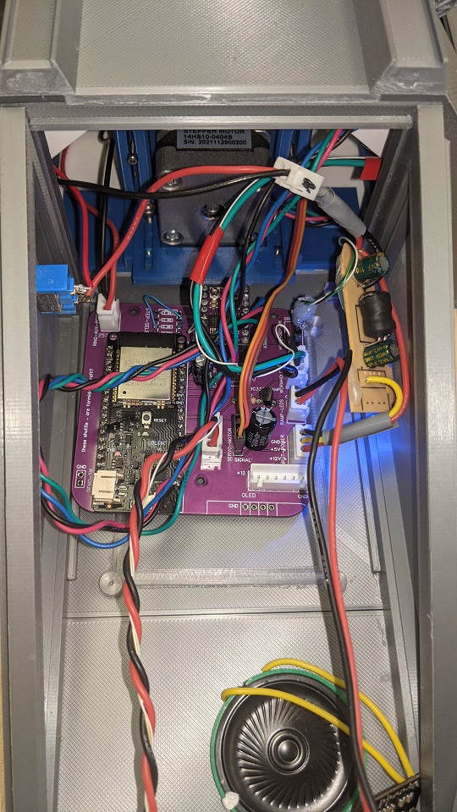
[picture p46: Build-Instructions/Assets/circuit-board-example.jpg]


The OLED screen is not mandatory

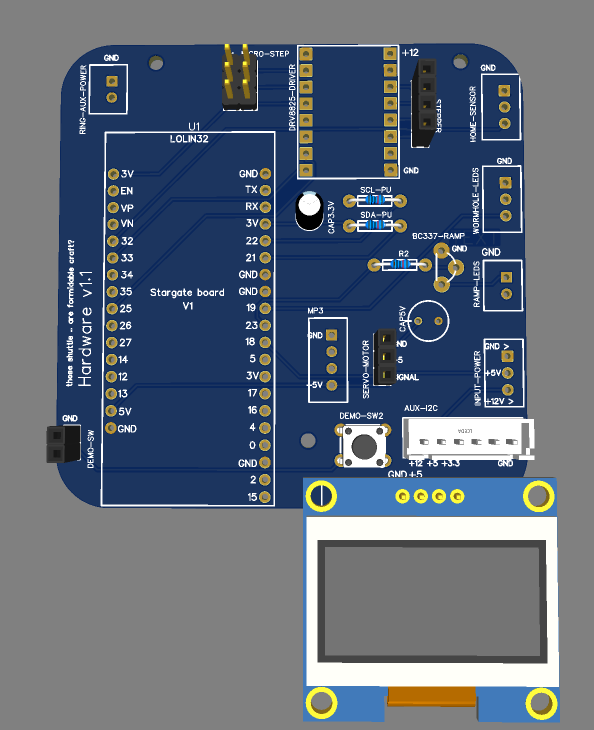
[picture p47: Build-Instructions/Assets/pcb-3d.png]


## Program the ESP32

***Warning:*** This chapter won't explain how to program an ESP32, there are plenty of existing tutorial to explain it.

- Connect a USB cable to the base ESP32.
- Flash "ring-fw" app into it.
- Connect to "SGU-Base-XXXXXX" Wi-Fi access point without password.
- Access to http://192.168.66.1 using a browser. You should get access to the control program.

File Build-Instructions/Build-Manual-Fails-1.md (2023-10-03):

# Failed prototypes

Many attempts were made before making a functional version. There is a small list of failed prototypes in case you are curious.

## Slip ring attempt

The first attempt used an home made slip ring with 3 tracks, one for GROUND, one for POSITIVE, one for SIGNAL.<br>
It used cooper tape for conductive track, the middle track is also used to guide bearings.<br>
It didn't work because it created too much friction, I tried make my own brushes by cutting graphite but it was a fail. Also conductive glue is<br> surprizingly hard to find or ridiculously expensive so my attempt to make my own conductive glue as also a failure.<br>

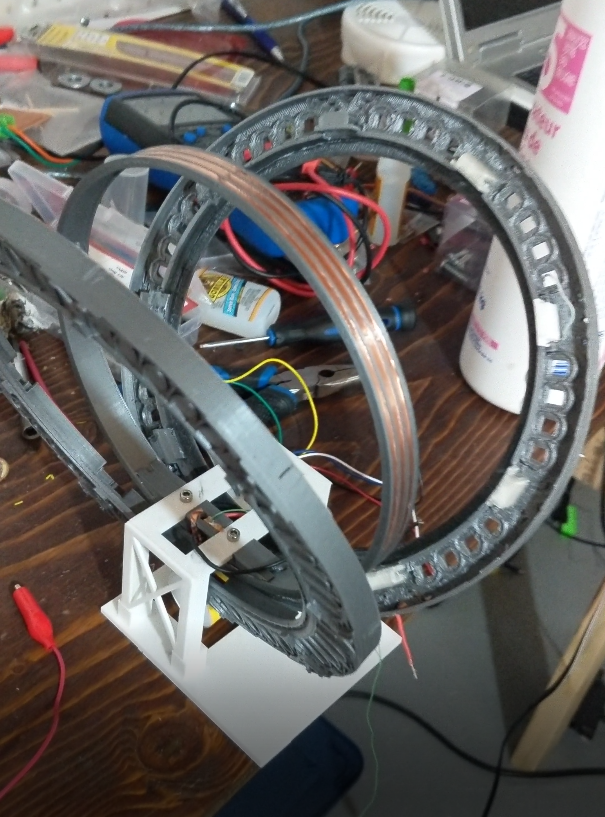
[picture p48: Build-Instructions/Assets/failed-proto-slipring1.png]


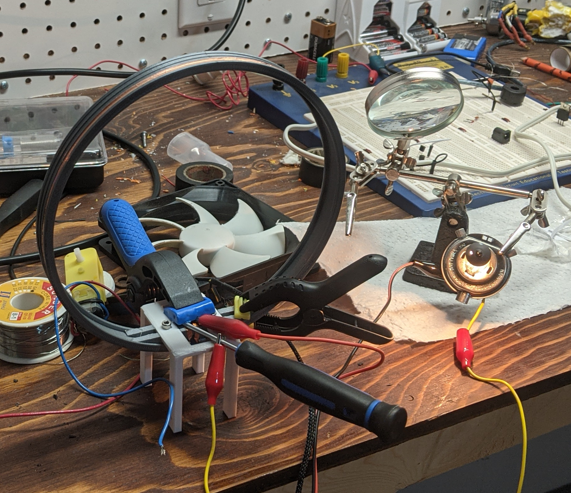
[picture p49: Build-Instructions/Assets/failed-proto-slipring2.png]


## Powered by induction

We successfully lighted up a LED for a few minute then it stopped and never worked again. Anyway it was doomed to fail, we probably just created an illegal emitter by accident in the end.

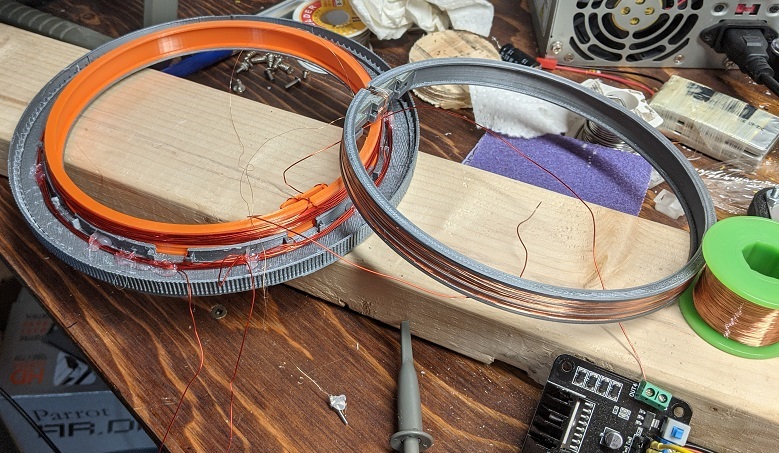
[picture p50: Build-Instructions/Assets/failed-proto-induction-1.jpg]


## Friction wheel

Because I couldn't resolve myself to deface the back of the gate by putting a visible gear there I tried using different friction materials with a wheel.

Using TPU:

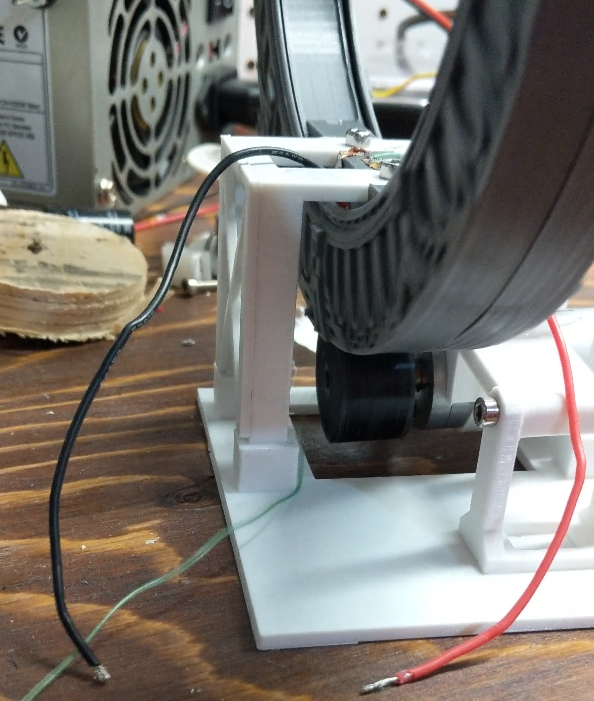
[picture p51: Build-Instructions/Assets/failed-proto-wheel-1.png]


Using sanding paper:

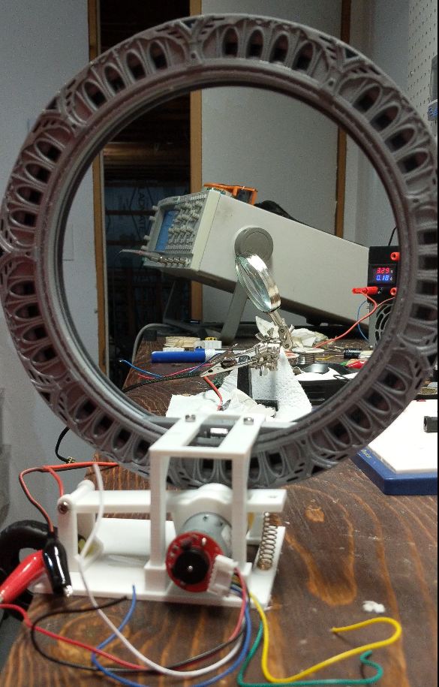
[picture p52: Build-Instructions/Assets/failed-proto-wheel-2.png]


## With bearing outside the ring

This one is an epic fail, it could barely hold itself and was ridiculously shacky.

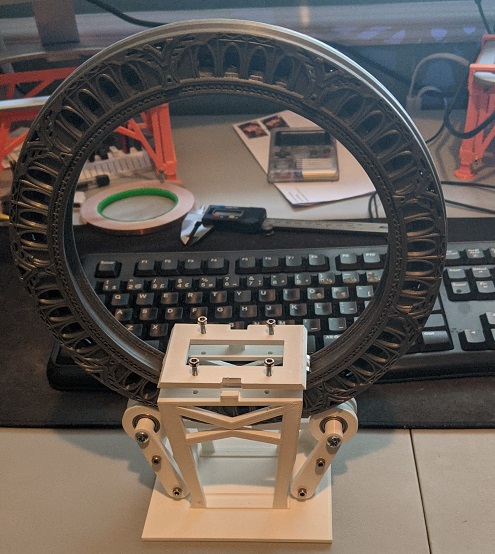
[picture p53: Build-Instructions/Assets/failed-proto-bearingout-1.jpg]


## Use a DC motor

The motor had backlash and not enough mechanical stiffness. Also the encoder didn't have a good resolution.<br>
Stepper with 1/16 steps does a better job.

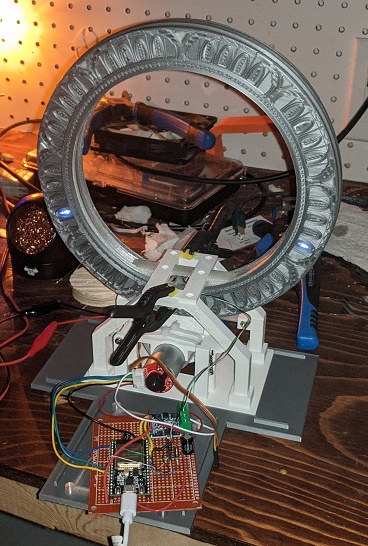
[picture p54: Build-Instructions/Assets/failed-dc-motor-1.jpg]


## Plunger inside the gate

I wasn't willing to have visible power contact on the backside so I wanted to be able to power recharge using an hidden plunger that connect to the electrical contact hidden inside the ring.

In the end I betrayed my conviction after it proved too difficult.

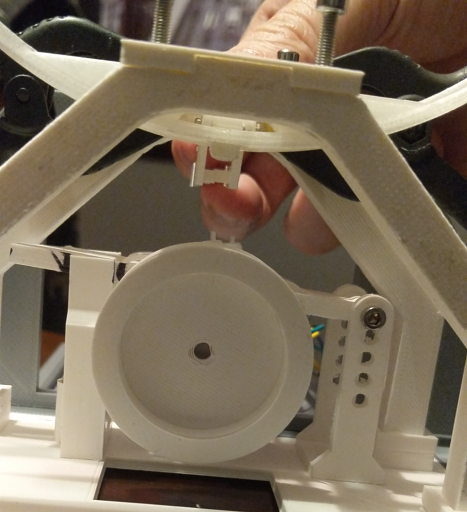
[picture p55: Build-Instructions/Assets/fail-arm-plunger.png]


## Node-MCU

I used a Node-MCU from Aliexpress but it was prone to brown-out. It maybe related to 5V regulator issues.
Still it got replaced by a Lolin32.

## Servo-Motor

I used cheap servo motor for the mecanism but it burned out after a few use. It got replaced by another cheap of the same kind because I didn't have anything else. Months later it still hold.

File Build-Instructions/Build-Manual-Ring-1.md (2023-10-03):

# Ring assembly

- Print "Stargate-Front-0.2mm_x1.stl" using 0.2 mm nozzle. Recommend using Tree Support with BRIM, no raft. May takes ~40h to print.

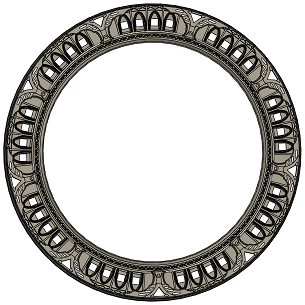
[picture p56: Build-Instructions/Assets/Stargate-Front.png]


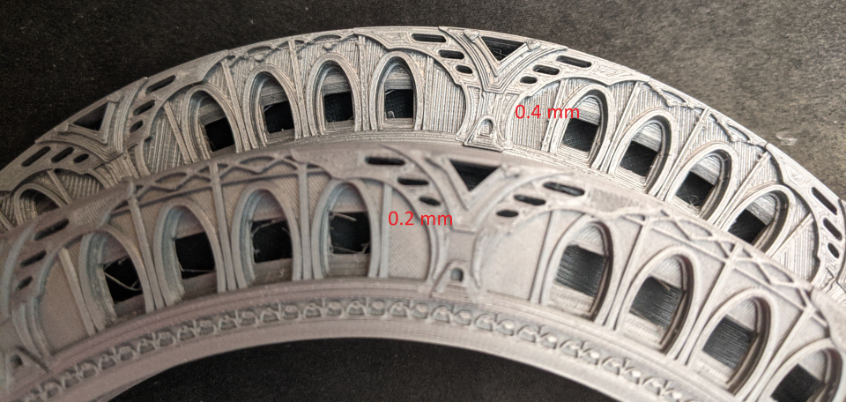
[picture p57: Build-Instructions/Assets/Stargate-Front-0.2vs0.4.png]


- Print "Stargate-Back-0.2mm_x1.stl" using 0.2 mm nozzle . Recommend using Tree Support with BRIM, no raft. May takes ~40h to print.

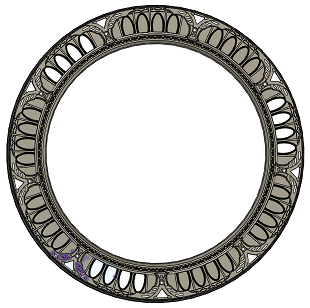
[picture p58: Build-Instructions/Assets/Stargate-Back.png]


- Print "Light-chevron-0.2mm_x18" 18 times using 0.2 mm nozzle

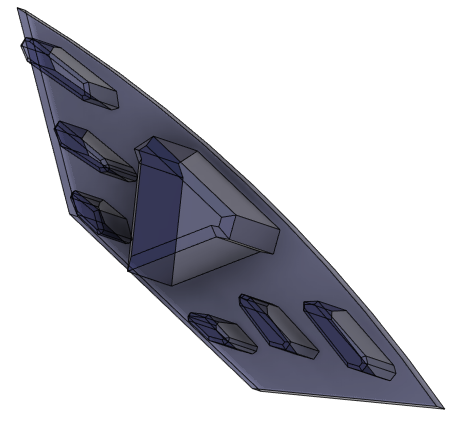
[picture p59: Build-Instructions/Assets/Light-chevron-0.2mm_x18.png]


- Print "Alignment-block-0.2mm_x9" 9 times using 0.2 mm nozzle

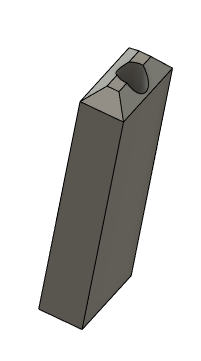
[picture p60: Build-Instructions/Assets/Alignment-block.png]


- Print "Module-With_wheel-0.2mm_x18.stl" 18 times using 0.2 mm nozzle. Color doesn't matter.



- Print "Light-chevron-cover-0.2mm-x9" 9 times using 0.2 mm nozzle. Using white PLA, it will reflect light.



- Print "Stargate-Back-TransWindow-0.2mm-x10-12" 12 times using 0.2 mm nozzle. Use transparent PLA or white.



- Print "Stargate-Back-Transparent-ResetBtn_0.2mm-x1" 1 time using 0.2 mm nozzle. Use transparent PLA or white.



- Print "Stargate-Back-Transparent-PwrSw_0.2mm-x1" 1 time using 0.2 mm nozzle. Use transparent PLA or white.



- Print "Magnet-ring" 1 times using 0.2 mm nozzle. Color doesn't really matter.



- Print "symbol-light-guide_0.2mm-x36.stl" 36 times using 0.2 mm nozzle. Should use transparent or white PLA.



- Print every symbols 1 times using 0.2 mm nozzle. Should use gray PLA.
You can use a resin printer to print them and get better resolution, but resin is more transparent than gray PLA. You will need to paint the symbols after if you want correct effect using resin or too much light will go through.



- Print "Inner ring" 1 times using 0.4 mm nozzle. Color doesn't really matter.



- Print "Inner-ring-sensor-holder_0.4mm-x1" 1 times using 0.4 mm nozzle. Color doesn't really matter.



- Print "Home-magnet-holder_0.4mm-x1" 1 times using 0.4 mm nozzle. Color doesn't really matter.



## Assemble alignment block and chevrons light diffuser

Use this picture as reference:



# Lightning diffuser for chevrons

- Insert "Light-Chevron" into place on "Stargate-Front" and "Stargate-Back".<br>
You may need a hammer and a big metal part to force it.<br>
Be gentle to not destroy the parts. You can print "Chevron-insert-tool.stl" too to help.

# Alignment blocks

- Insert "Alignment-block" into place on the "Stargate-Front" part.
Ensure the holes are clear and everything fit. Then glue them in place, pour gorilla glue into the hole then install the alignment blocks.
- Use a sharpie and mark a chevron as being the "master chevron" on both side. Doesn't matter which one it is but it should have a master chevron. It's labelled M.C on the picture above, use the same pattern.

# Test

- Try to assemble "Stargate-Front" and "Stargate-Back" together to ensure alignment block are meshing together.



# Assemble bearing modules

- Ordered bearing comes with not so great grease, put some WD40 or Jig-A-Loo into bearings. Be careful, Jig-A-Loo attack PLA a little bit, if you clean the part with a towel the color of the PLA stain the paper so ...
- Modules are made of two parts meant to mesh together and hold the bearing in sandwitch.
The part is printed 18 times so you will have 9 modules.
Tolerances are very tight, you will have to use a lot of force to insert the bearing. If it's not hard to insert then something is wrong and you may need to change the design of the part or trying print it with lower resolution. We suggest you to use a wrench or c-clamp to force two part together.
- Use gorilla glue to glue both part together and use clamp to hold parts





- Insert the completed modules in their final spaces to ensure everything fit in place.

***Warning***: DO NOT GLUE THE MODULES to the stargate-back or stargate-front! they will never need to be glued. They will hold in place by themselve once both halves get assembled.



# Assemble symbols

Tolerances are so tight that you will need a hammer to insert symbols in place and you need to put something behind the gate to avoid destroying it.
You don't need glue. It may be possible you need to sand a bit to insert symbols.

- Put each "symbol-light-guide_0.2mm-x36" (36 of them) into symbol holes. You can try lighting up a LED behind to ensure they diffuse light correctly.



- Insert symbols in each holes at correction positions according to the chart, the master chevron should be positionned as top most according to your previous marking.







# Assemble lights reflectors (Light-chevron-cover)

The reflectors are meant to reflect light and give a better effect so it's important to print them with white color.

- Glue "light-chevron-cover" using canopy glue over chevron "Light-chevron".
- Glue WS2812B leds over holes, there are 45 LEDs to glue using canopy glue. It's important for chevron LEDs to be as close as possible to "alignment-block" and not interfere with the ring groove. Magnet ring will be fitted there later. ** WARNING: ** There is an arrow on each LEDs, they should point in counter-clockwise direction. (See the picture)
- Starting with the "master chevron" LED, solder all LEDs positive and negative terminals. Ensure to connect the last LED to the master chevron LED to reduce voltage peak. You can use nacked wire. **Warning: ** Ensure to not overheat with the soldering iron. Be very careful to not melt the plastic under it.
- Starting with the "master chevron" LED, solder every data wire, start with the output of the master chevron LED, then connect to the next etc ...
The master chevron LED data input should be where the microcontroller will be connected later. Recommend to use very small gauge, like 28 awg.



- Add tape over symbols LEDs to project from accidental short circuit.
- Add a 3 pins connector on the master chevron LED. Servo motor connector or JST can do the job. One ground, one positive and the WS2812B led data input.



# Assemble stargate back window

You needs those parts:
- Stargate-Back-TransWindow-0.2mm-x10-12.stl (x1)



- Stargate-Back-Transparent-ResetBtn_0.2mm-x1.stl (x1)



- Stargate-Back-Window-pushbutton_0.2mm-x1.stl (x10)



### Power collector

- Use two "Stargate-Back-TransWindow-0.2mm-x10-12", wrap them using cooper tape.
** Warning: ** The back of the cooper tape is not conductor at all, ensure both side are covered by the same piece.
- Glue them in place using gorilla glue
- Use a sharpy to mark the positive and the negative inside the ring.
- Insert the magnet into "Home-magnet-holder_0.4mm-x1" and glue it in place on "stargate-back" (check the photo for details)

Hall sensor are sensitive to polarity, so you need to test it before attempting to insert it in place.



- Mark polarity inside the track using a sharpie. It won't be visible once assembled.



### Other windows

- Glue other transparent window and buttons using this pattern.





# Magnetic ring

Odd position magnets should not have the same polarity as even magnets.
**WARNING** We recommend to install the magnet ring into the "stargate-front" part and glue it in place before installing magnets.
Don't glue it too hard, just tacking is good enough as long as the magnets cannot move outside.

- Use the stack of magnets and put them in place starting from the top most magnets, skip one position every time.
- Flip the stack of magnets and put reverted polarity magnet into remaining holes.
- You can add some canopy glue over magnets to hold them in place. Not too much.

The photo doesn't show it installed inside the "stargate-front" because I don't have any photo of it.



This photo comes from an ealier prototype, as you can see there is no location for modules on it but if you check the magnet ring inside the groove it should looks like this when assembled with all magnets in place.







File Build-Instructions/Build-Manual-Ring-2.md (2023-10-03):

# Internal electronic

## Solder and assemble

- Solder the header necessary to easily program the M5Stamp Pico. The header should be accessible when the ring is disassembled.



- Install batteries using hot glue. You don't need to put a lot, just tacking is good enough.



- Assemble the electronic according to this picture: (You have no obligation to position the parts this way, but ensure to balance weight as much as possible)
** Warning: ** Unfortunately there are not a lot of picture of this part. Earlier you installed a connector for WS2812B leds, you will have to soldier the other half of the connector according to the plan.





## Prime the gate

To start, the gate ring to receive power from power collector (DON'T REVERSE POLARITY!) at least to start, then the ESP32 can hold it's own power using the MOSFET. But if you power it using the programmer it will stay powered.

## Program the M5Stamp Pico

***Warning:*** This chapter won't explain how to program an ESP32, there are plenty of existing tutorial to explain it.

You need to use the ESP-IDF 5.1 toolkit to compile and program the 'ring-factory' software into the M5Stamp. The software allows to upload the real firmware over the air without using any electronical connection.

It wouldn't be very practical if it was required to dissamble the ring everytime a firmware upgrade is necessary.

The bootloader of the factory app is programmed to automatically erase the last firmware if you hold the button for 5s after startup.
You can disconnect the battery using the toggle switch, hold the button, then prime the gate.

- You need to connect the M5Stamp pico programmer to the M5Stamp pico.
- Flash "ring-factory" app into it.
- Prime the ring or let it connected to the programmer, chevron should blink with a nice pattern.
- Connect to "SGU-Ring-Fact-XXXXXX" Wi-Fi access point without password.
- To flash it with the real firmware (ring-fw), use a browser and reach this address : http://192.168.66.1 . A webpage allows you to upload a new binary directly without hassle.

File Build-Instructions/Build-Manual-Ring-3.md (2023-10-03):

# Inner ring

## Sanding

- You need to sand the inner ring using 180 / 400 grid sandpaper, the middle track will be run over by the bearing.
the slighest flaw will make it works badly.



## Glue the bridge

- You will need gorilla glue, clamp and 10 mm M3 screw. M3 screw are only used for alignment, glue is what matter to hold parts together.



- It will look like this once glued:



- Once the glue is set, you can remove M3 screw and fill the hole with more glue.

## Install the inner ring into the ring

- Install the inner ring into the center, ensure it's in the right ring direction relative to the outer ring.
- Install bearing modules in place
- Number bearing module with sharpie starting from the master chevron as #1, go counter-clockwise. Mark again the master chevron anywhere it could help.



I hope you didn't glue the bearing module in place
It should looks like this:



## Install the hall sensor

**WARNING:** Ensure to install the hall sensor the right way, it is sensitive to magnet polarity.
 - Find the part "Inner-ring-sensor-holder"
 - Solder wire to the hall sensor, label or use recornisable color to differentiate power and signal.
 - Ensure to find the right hall sensor direction so it could react with the magnet inside the ring 2Home-magnet-holder"
    - We suggest you to test it with an arduino or something.
 - Glue the part and the sensor at the right place (check the picture)





## Install screws

This step is necessary to ensure the gate spin correctly before going further.
You will need to screw both halves in place using M2x15 screws (shorter can do it too).

There are 9 screws that fit in the back of the gate.



### Ensure it spins

Try to make it spins freely, if required sand again the inner-ring or the edge of the outer-ring.
If everything is fine, continue to next step but you will need to remove screw later.



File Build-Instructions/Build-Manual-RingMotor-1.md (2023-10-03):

# Ring/base assembly

The design is relatively modular so you can make your own base if you want as long as the ring assembly fit into it.
It is partly designed as base and ring so I decided to create a specific chapter for this part.

## Instructions

- Glue "Truss#1_4mm-x1.stl" and "Truss#1_4mm-x2.stl" anywhere (check the picture). It's the same part.
Use Gorilla Glue, it's a structural part.



## Install the ring to the base

Use nuts to install the ring to the base. It allows to easily remove the ring later if necessary.

### Required parts

- "Bottom-plate-v2_4mm-x1.stl", "Truss#1_4mm-x1.stl" and "Truss#2_4mm-x1.stl".
- 4x M3x15 screws but as long as it fit it's fine it could be longer too.
- 4x M3 nuts





# Stepper-mount

## Install hidden nuts

This part is tricky because it may be required to use a lighter to insert M3 nuts into place.
If M3 nuts fit you can just fit them with force, but if it doesn't you can use the longest possible M3 screw you can find, install the M3 nuts to it, then use a lighter to heat the nut then push very hard on the plastic part to force it to enter. It will make the nuts fit perfectly and stay in place without using glue.<br>
You can also use a soldering iron to push on the nut but you need to be careful to not overheat.



## Glue to the bottom plate

Using Gorilla Glue, glue "Stepper-mount-1_4mm-x1.stl" to the "Bottom-plate-v2_4mm-x1.stl".<br>
Use clamp to hold the part in place and ensure glue won't go into the nuts.





# Install the stepper in place

## Install "Stepper-bracket_4mm-x1.stl" on NEMA14 stepper

Use 4x M3x10 screws to install the stepper bracket on the stepper.





## Install "Stepper-mount-1_4mm-x1.stl" to "Stepper-mount-2_4mm-x1.stl"

Use 4x M2x15 screw and 4x M2 nuts to install to hold both parts together.<br>
This part allows to adjust the bracket by loosing nuts.





## Prepare the magnetic gear

Use 4x2 mm magnet, push them into place using a screwdriver. Magnet should stay there by themselves, there is a small nudge to hold them.<br>
Odd position magnet and even position magnet shall have different polarity or it's not going to work. If you make a mistake there are hole behind the gear to push magnet out. If magnet have difficulty to hold in place you can drip some canopy glue or hot glue into the holes.



## Install the magnetic gear on the stepper

You may need to hammer the back of the shaft of the stepper until the gear press-fit into place. You may have to reajust later if it's not correct but the stepper can easily be removed to work on it.<br>
***WARNING:*** Hit the shaft, not the back of the stepper or you risk damaging to the stepper.





## Install "Stepper-mount-2_4mm-x1.stl" on "Bottom-plate-v2_4mm-x1.stl"

Use 4x 3Mx8 to install to the bottom plate. You can use only 2x 3Mx8 if you think it's enough.





It should looks like this in the end.



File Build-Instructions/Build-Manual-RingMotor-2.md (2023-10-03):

# Ring/base assembly

Install the power plunger. It allows to recharge the gate and keep it active when the master chevron is at the top.

## Install anchors (Back-plunger-anchor_4mm-x2.stl)

Ensure M3 nuts can fit into the back of each anchor. If it doesn't, just heat it in place with a solder iron until it fit.



Use Gorilla glue to glue both anchor into place.



## Assemble "back-plunger"

Glue "Back-plunger-bar_4mm-x1.stl" and "Back-plunger-Higher-spring_4mm-x1.stl" together using Gorilla glue.



## Assemble "Back-plunger-arm_4mm-x1.stl"

- You needs to wrap each contactor with cooper tape.
- The left side (relative to the view on the picture) should be soldered to the ground, on a black wire if possible. The wire should be flexible, sillicon is the best.
- The right side should be soldered to positive (+5v). The wire should be flexible, sillicon is the best.

***WARNING:*** Don't heat too much, you should do it quickly to not melt the plastic.



Glue "Back-plunger-Higher-spring_4mm-x1.stl" to "Back-plunger-arm_4mm-x1.stl" using Gorilla glue.



Install a 4 mm by 30 mm spring, we used one coming from a pen. If it's too long you can cut it.

## Install the arm

Use two M2x20 screw to install the arm, shouldn't be too tight, the arm shoud be free to move.



## Glue the servo motor on (Back-plunger-bar_4mm-x1.stl)

Use canopy glue or gorilla glue to glue the servo to "Back-plunger-bar_4mm-x1.stl". Use a clamp to hold it in place.



## Glue the hammer (black-plunger-hammer_4mm-x1.stl, black-plunger-hammer-cover_4mm-x1.stl) to the servo arm

You may need to do some modification to your servo arm, there are difference between models.



## Install "Back-plunger-arm_4mm-x1.stl" in place

You just need to use 2 M3x10 screws to install the part in place.







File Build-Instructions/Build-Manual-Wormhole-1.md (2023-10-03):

# Wormhole

## Cut the plexiglass

You need a 2 mm sheet of plexiglass. Be carefull with compass, it could leave horrible traces.

You need to cut circle of 161.5 mm into a plexiglass sheet.
You will need to cut the lower part at the right height using a dremel or use "Plexgliass-Template-Dummy.stl" as template for laser cut.

- Ensure the plexiglass part fit into "Inner-ring-0.4mm_x1.stl". You shouldn't need to force to insert it to should fit easily. Sand a little bit if necessary. DON'T GLUE IT YET !

## Apply half-way mirror film

Remove the plastic protection on the mirror film, it could be a nightmare to find but it's there.
You cannot apply it directly to the plexiglass, it won't work it will just create something horrible full of bubble and ruin your nice work.
You can check on youtube there are several tutorial about how to apply it but basically you need:
- Cut the film, it should be 1 inch bigger on every side. Ensure you get a nice spot, sometime the film could be slighly damaged. Inspect just to be sure.
- Apply water mixed with soap using a spray bottle over the plexiglass
- Remove the protection film from the mirror film
- Stick the mirror film over the plexiglass, use a ruler to push water bubble ouside

## Glue the plexiglass to "Inner-ring-0.4mm_x1.stl"

The ring shouldn't be assembled, you need to remove 9 allens screws behind the ring.

- Glue the plexiglass to the inner ring using canopy glue.





## Glue LEDs in place on "Wormhole.stl"

Use canopy glue to glue all leds in place. Use a sharpie to write each LEDs number. It is not visible so it's not really a problem.

LEDs 47 and 48 are missing on this photo because we didn't plan to use them but we did in the end.



## Solder leds

As you can see it's not perfectly optimized, because 47 and 48 were planed to not be installed but were in the end. But if you want to use a better pattern you can you will just need to slightly change the code to make it works.



## Glue the filter

The filter "Wormhole-filter.stl" is just a white PLA filter to diffuse light and make it more uniform. It is recommended to test it for real before gluing.
If you are ready to glue the filter, then you shouldn't use canopy glue because capilarity make glue do where it shouldn't.

It's not a structural part, it doesn't need an incredible bond so you can just use hot glue and spread it using a toothpick.

Example of ruined filter:



## Glue "Wormhole-outer-rim.stl"

Glue it using gorilla glue on the outside part of the "Wormhole-outer-rim.stl".
Use clamp to be sure it hold in place until glue is completely cured.



## Glue "Wormhole.stl" to "Wormhole-outer-rim.stl"

Glue wormhole behind the outer rim using canopy glue but not too much to be sure it will not drip where it shouldn't.
You don't need to put a lot of glue, a few spot is more than enough it's not a structural part also it could be useful to not overglue if you need to dismantle it later.



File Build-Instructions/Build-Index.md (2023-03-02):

# Table of contents
1. Before building
    1. [Material prerequisite](Build-Manual-0.md)
    2. [Recommendation](Build-Manual-1.md)
    3. [Introduction to the destiny gate](Gate-Intro.md)
2. Build the base
    1. [Base assembly #1](Build-Manual-Base-1.md)
    2. [Base assembly #2](Build-Manual-Base-2.md)
    3. [Base electronic](Build-Manual-Base-3.md)
3. Build the ring
    1. [Ring assembly #1](Build-Manual-Ring-1.md)
    2. [Ring internal electronic #2](Build-Manual-Ring-2.md)
    3. [Ring Inner ring #3](Build-Manual-Ring-3.md)
4. Assemble the ring and base together
    1. [Ring base assembly #1](Build-Manual-RingMotor-1.md)
    2. [Ring base assembly #2](Build-Manual-RingMotor-2.md)
5. [Software](Build-Manual-Software-1.md)
6. [Wormhole](Build-Manual-Wormhole-1.md)

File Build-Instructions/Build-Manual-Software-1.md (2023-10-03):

# Software

## URL

| Description | URL |
|---|---|
| Home page of the system | http://192.168.66.1/index.html
| Get many system informations | http://192.168.66.1/about-ota.html
| Get current settings (JSON) | http://192.168.66.1/settings.html

## About-OTA

Give system informations and it allows to upload over-the-air (OTA) update

## Settings

You can get JSON settings by browsing at : ./settings.html
If you want to change settings, you can use insomnia or postman to POST your new JSON file at: ../api/setsettingsjson

## Mp3 Player

DF Robot Mini Pro (DF1201S). It has it's own USB drive so you can plug it to a computer and upload whatever you want.



The only way we have found to play a specific file (the provided command for playing by name doesn't work) is
to use the file number. It is defined by copy order on the USB drive.

To add sound FX to the mp3 player:
- Connect it to a computer
- Access to the USB drive
- Locate .\SoundFX\copy.bat edit it to replace by the right drive letter



- Execute it.
- Ensure all files were copied on the USB drive. If you screw the order you can format it and do the procedure again.



## Index

Allows to control the gate, dial address or manually activate/deactivate lightning.




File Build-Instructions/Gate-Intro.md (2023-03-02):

# How it works?

SG1 and SGA gate use constellation like glyth (or symbols). Unlike these, the Stargate Universe Gate uses some kind of numeral because it travel through different galaxies.

Copyright: https://stargate.fandom.com/wiki/Glyph#Milky_Way_glyphs

There are 36 symbols + 9 chevrons

| Position | Symbols | Position | Glyph | Position | Symbols |
|---|---|---|---|---|---|
| 1	 |  | 13 |  | 25 | 
| 2	 |  | 14 |  | 26 | 
| 3	 |  | 15 |  | 27 | 
| 4	 |  | 16 |  | 28 | 
| 5	 |  | 17 |  | 29 | 
| 6	 |  | 18 |  | 30 | 
| 7	 |  | 19 |  | 31 | 
| 8	 |  | 20 |  | 32 | 
| 9	 |  | 21 |  | 33 | 
| 10 |  | 22 |  | 34 | 
| 11 |  | 23 |  | 35 | 
| 12 |  | 24 |  | 36 | 

# Stargate Layout

From Joseph Malozzi blog:



Final layout in the serie:



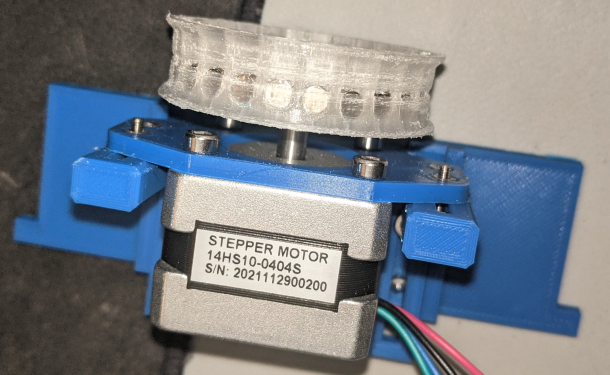
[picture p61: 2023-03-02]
Build-Instructions/Assets/magnet-gear-with-magnet.png

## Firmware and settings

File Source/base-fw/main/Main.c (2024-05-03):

/*  WiFi softAP Example

   This example code is in the Public Domain (or CC0 licensed, at your option.)

   Unless required by applicable law or agreed to in writing, this
   software is distributed on an "AS IS" BASIS, WITHOUT WARRANTIES OR
   CONDITIONS OF ANY KIND, either express or implied.
*/
#include <string.h>
#include <time.h>
#include "freertos/FreeRTOS.h"
#include "freertos/task.h"
#include "esp_system.h"
#include "esp_wifi.h"
#include "esp_event.h"
#include "esp_log.h"
#include "esp_mac.h"
#include "nvs_flash.h"
#include <esp_event.h>
#include <esp_log.h>
#include <esp_sntp.h>
#include "lwip/err.h"
#include "lwip/sys.h"
#include "webserver/WebServer.h"
#include "lwip/apps/netbiosns.h"
#include "GPIO.h"
#include "FWConfig.h"
#include "Settings.h"
#include "Main.h"
#include "GateControl.h"
#include "GateStepper.h"
#include "SoundFX.h"
#include "SSD1306.h"

/* The examples use WiFi configuration that you can set via project configuration menu.

   If you'd rather not, just change the below entries to strings with
   the config you want - ie #define EXAMPLE_WIFI_SSID "mywifissid"
*/

static const char *TAG = "wifi";

SGUBRCOMM_SHandle g_sSGUBRCOMMHandle;
static SGUBRCOMM_SSetting m_sSetting = { .eMode = SGUBRCOMM_EMODE_Base };
static TickType_t m_xRebootRequestTicks = 0;
static char m_szSoftAPSSID[31] = {0,};

static esp_netif_t* m_pWifiSoftAP;
static esp_netif_t* m_pWifiSTA;

static void wifi_init_all(void);
static void wifi_init_softap(void);

static void wifi_event_handler(void* arg, esp_event_base_t event_base, int32_t event_id, void* event_data);
static void wifistation_event_handler(void* arg, esp_event_base_t event_base, int32_t event_id, void* event_data);

static void PrintCurrentTime();

static void time_sync_notification_cb(struct timeval *tv);

static void wifi_event_handler(void* arg, esp_event_base_t event_base, int32_t event_id, void* event_data)
{
    if (event_id == WIFI_EVENT_AP_STACONNECTED) {
        wifi_event_ap_staconnected_t* event = (wifi_event_ap_staconnected_t*) event_data;
        ESP_LOGI(TAG, "station %02x:%02x:%02x:%02x:%02x:%02x join, AID=%d",
                 event->mac[0], event->mac[1],event->mac[2], event->mac[3],event->mac[4], event->mac[5],
                 (int)event->aid);
    } else if (event_id == WIFI_EVENT_AP_STADISCONNECTED) {
        wifi_event_ap_stadisconnected_t* event = (wifi_event_ap_stadisconnected_t*) event_data;
        ESP_LOGI(TAG, "station %02x:%02x:%02x:%02x:%02x:%02x leave, AID=%d",
                 event->mac[0], event->mac[1],event->mac[2], event->mac[3],event->mac[4], event->mac[5],
                 (int)event->aid);
    }
}

static void wifistation_event_handler(void* arg, esp_event_base_t event_base, int32_t event_id, void* event_data)
{
    if (event_base == WIFI_EVENT && event_id == WIFI_EVENT_STA_START) {
        esp_wifi_connect();
     }
     else if (event_base == WIFI_EVENT && event_id == WIFI_EVENT_STA_CONNECTED ) {
        ESP_LOGI(TAG, "Connected to the AP");
        esp_netif_create_ip6_linklocal(m_pWifiSTA);
     } else if (event_base == WIFI_EVENT && event_id == WIFI_EVENT_STA_DISCONNECTED) {
        esp_wifi_connect();
        ESP_LOGI(TAG, "connect to the AP faile, retry to connect to the AP");
    } else if (event_base == IP_EVENT && event_id == IP_EVENT_STA_GOT_IP) {
        ip_event_got_ip_t* event = (ip_event_got_ip_t*) event_data;
        ESP_LOGI(TAG, "got ip:" IPSTR, IP2STR(&event->ip_info.ip));
    } else if (event_base == IP_EVENT && event_id == IP_EVENT_GOT_IP6) {
        ip_event_got_ip6_t *event = (ip_event_got_ip6_t *)event_data;
        ESP_LOGI(TAG, "Got IPv6 address " IPV6STR, IPV62STR(event->ip6_info.ip));
    }
}

static void wifi_init_all(void)
{
    wifi_init_config_t cfg = WIFI_INIT_CONFIG_DEFAULT();
    ESP_ERROR_CHECK(esp_wifi_init(&cfg));

    const bool isWiFiSTA = NVSJSON_GetValueInt32(&g_sSettingHandle, SETTINGS_EENTRY_WSTAIsActive) == 1;
    if (isWiFiSTA)
    {
        ESP_ERROR_CHECK(esp_wifi_set_mode(WIFI_MODE_APSTA) );
    }
    else
    {
        ESP_ERROR_CHECK(esp_wifi_set_mode(WIFI_MODE_AP) );
    }

    // Access point mode
    m_pWifiSoftAP = esp_netif_create_default_wifi_ap();

    esp_netif_ip_info_t ipInfo;
    IP4_ADDR(&ipInfo.ip, 192, 168, 66, 1);
	IP4_ADDR(&ipInfo.gw, 192, 168, 66, 1);
	IP4_ADDR(&ipInfo.netmask, 255, 255, 255, 0);
	esp_netif_dhcps_stop(m_pWifiSoftAP);
	esp_netif_set_ip_info(m_pWifiSoftAP, &ipInfo);
	esp_netif_dhcps_start(m_pWifiSoftAP);

    ESP_ERROR_CHECK(esp_event_handler_instance_register(WIFI_EVENT,
                                                        ESP_EVENT_ANY_ID,
                                                        &wifi_event_handler,
                                                        NULL,
                                                        NULL));

    wifi_config_t wifi_configAP;
    memset(&wifi_configAP, 0, sizeof(wifi_configAP));
    //wifi_configAP.ap.channel = FWCONFIG_SOFTAP_WIFI_CHANNEL;
    strcpy((char*)wifi_configAP.ap.password, FWCONFIG_SOFTAP_WIFI_PASS);
    wifi_configAP.ap.max_connection = FWCONFIG_SOFTAP_MAX_CONN;
    wifi_configAP.ap.authmode = WIFI_AUTH_WPA_WPA2_PSK;

    uint8_t macAddr[6];
    esp_read_mac(macAddr, ESP_MAC_WIFI_SOFTAP);

    sprintf((char*)wifi_configAP.ap.ssid, FWCONFIG_SOFTAP_WIFI_SSID_BASE, macAddr[3], macAddr[4], macAddr[5]);
    strcpy((char*)m_szSoftAPSSID, (char*)wifi_configAP.ap.ssid);

    int n = strlen((const char*)wifi_configAP.ap.ssid);
    wifi_configAP.ap.ssid_len = n;

    if (strlen((const char*)FWCONFIG_SOFTAP_WIFI_PASS) == 0) {
        wifi_configAP.ap.authmode = WIFI_AUTH_OPEN;
    }

    ESP_ERROR_CHECK(esp_wifi_set_config(WIFI_IF_AP, &wifi_configAP));

    // Soft Access Point Mode
    ESP_LOGI(TAG, "wifi_init_softap finished. SSID:%s password:%s channel:%d",
             wifi_configAP.ap.ssid, FWCONFIG_SOFTAP_WIFI_PASS, (int)FWCONFIG_SOFTAP_WIFI_CHANNEL);

    if (isWiFiSTA)
    {
        m_pWifiSTA = esp_netif_create_default_wifi_sta();

        esp_event_handler_instance_t instance_any_id;
        esp_event_handler_instance_t instance_got_ip;
        esp_event_handler_instance_t instance_got_ip6;
        ESP_ERROR_CHECK(esp_event_handler_instance_register(WIFI_EVENT,
                                                            ESP_EVENT_ANY_ID,
                                                            &wifistation_event_handler,
                                                            NULL,
                                                            &instance_any_id));

        ESP_ERROR_CHECK(esp_event_handler_instance_register(IP_EVENT,
                                                            IP_EVENT_STA_GOT_IP,
                                                            &wifistation_event_handler,
                                                            NULL,
                                                            &instance_got_ip));
        ESP_ERROR_CHECK(esp_event_handler_instance_register(IP_EVENT,
                                                            IP_EVENT_GOT_IP6,
                                                            &wifistation_event_handler,
                                                            NULL,
                                                            &instance_got_ip6));

        wifi_config_t wifi_configSTA;
        memset(&wifi_configSTA, 0, sizeof(wifi_configSTA));
        //wifi_configSTA.sta.threshold.authmode = WIFI_AUTH_OPEN;
        wifi_configSTA.sta.threshold.authmode = WIFI_AUTH_WPA_PSK;
        wifi_configSTA.sta.sae_pwe_h2e = WPA3_SAE_PWE_BOTH;

        size_t staSSIDLength = 32;
        NVSJSON_GetValueString(&g_sSettingHandle, SETTINGS_EENTRY_WSTASSID, (char*)wifi_configSTA.sta.ssid, &staSSIDLength);

        size_t staPassLength = 64;
        NVSJSON_GetValueString(&g_sSettingHandle, SETTINGS_EENTRY_WSTAPass, (char*)wifi_configSTA.sta.password, &staPassLength);

        ESP_LOGI(TAG, "STA mode is active, attempt to connect to ssid: %s", wifi_configSTA.sta.ssid);

        ESP_ERROR_CHECK(esp_wifi_set_config(WIFI_IF_STA, &wifi_configSTA) );
    }

    // Start AP + STA
    ESP_ERROR_CHECK(esp_wifi_start() );
}

void app_main(void)
{
    vTaskPrioritySet( NULL, FWCONFIG_MAINTASK_PRIORITY_DEFAULT);

    //Initialize NVS
    esp_err_t ret = nvs_flash_init();
    if (ret == ESP_ERR_NVS_NO_FREE_PAGES || ret == ESP_ERR_NVS_NEW_VERSION_FOUND) {
      ESP_ERROR_CHECK(nvs_flash_erase());
      ret = nvs_flash_init();
    }

    ESP_ERROR_CHECK(ret);

    SETTINGS_Init();

    NVSJSON_Load(&g_sSettingHandle);

    // Need to be high ...
    GPIO_Init();

    SOUNDFX_Init();

    GATESTEPPER_Init();

    ESP_ERROR_CHECK(esp_netif_init());
    ESP_ERROR_CHECK(esp_event_loop_create_default());

    ESP_LOGI(TAG, "wifi_init_all");
    // wifi_init_softap();
    wifi_init_all();

    sntp_setoperatingmode(SNTP_OPMODE_POLL);
    sntp_setservername(0, "pool.ntp.org");
    sntp_set_time_sync_notification_cb(time_sync_notification_cb);
    ESP_LOGI(TAG, "Initializing SNTP");
    sntp_init();

    GATECONTROL_Init();

    GATECONTROL_Start();

    strcpy(m_sSetting.dstRingAddress, FWCONFIG_RING_IPADDRESS);
    SGUBRCOMM_Init(&g_sSGUBRCOMMHandle, &m_sSetting);
    SGUBRCOMM_Start(&g_sSGUBRCOMMHandle);
    // GATECONTROL_DoAction(GATECONTROL_EMODE_GoHome);

    // const TickType_t xFrequency = 1;

     // Initialise the xLastWakeTime variable with the current time.
    // TickType_t xLastWakeTime = xTaskGetTickCount();
    TickType_t xLEDBlinkTicks = xTaskGetTickCount();
    TickType_t xPrintTimeTicks = 0;
    #ifdef HWCONFIG_OLED_ISPRESENT
    TickType_t xUpdateOLEDTicks = 0;
    #endif

    bool bAltern = false;

    WEBSERVER_Init();

    char* szAllTask = (char*)malloc(4096);
    vTaskList(szAllTask);
    ESP_LOGI(TAG, "vTaskList: \r\n\r\n%s", szAllTask);
    free(szAllTask);

    // Small delay to be sure the Mp3 player doesn't play random things before being started up.
    vTaskDelay(pdMS_TO_TICKS(500));
    SOUNDFX_Stop();

    while(true)
    {
        #ifdef HWCONFIG_OLED_ISPRESENT
        // Update OLED screen
        if ( (xTaskGetTickCount() - xUpdateOLEDTicks) > pdMS_TO_TICKS(250) )
        {
            SSD1306_handle* pss1306Handle = GPIO_GetSSD1306Handle();
            const char szText[128+1];

            esp_netif_ip_info_t wifiIpSta = {0};
            MAIN_GetWiFiSTAIP(&wifiIpSta);

            esp_netif_ip_info_t wifiIpAP = {0};
            MAIN_GetWiFiSoftAPIP(&wifiIpAP);

            sprintf(szText, "%s\n"IPSTR"\n"IPSTR,
                m_szSoftAPSSID,
                IP2STR(&wifiIpAP.ip),
                IP2STR(&wifiIpSta.ip));

            SSD1306_ClearDisplay(pss1306Handle);
            SSD1306_DrawString(pss1306Handle, 0, 0, szText, strlen(szText));
            SSD1306_UpdateDisplay(pss1306Handle);
            xUpdateOLEDTicks = xTaskGetTickCount();
        }
        #endif

        // Wait for the next cycle.
        vTaskDelay(pdMS_TO_TICKS(1));
        //vTaskDelayUntil( &xLastWakeTime, xFrequency );

        if ( (xTaskGetTickCount() - xLEDBlinkTicks) > pdMS_TO_TICKS(250) )
        {
            GPIO_SetSanityLEDStatus(bAltern);
            bAltern = !bAltern;
            xLEDBlinkTicks = xTaskGetTickCount();
        }

        if ( (xTaskGetTickCount() - xPrintTimeTicks) > pdMS_TO_TICKS(20*1000) )
        {
            PrintCurrentTime();
            xPrintTimeTicks = xTaskGetTickCount();
        }

        if (m_xRebootRequestTicks != 0 && (xTaskGetTickCount() - m_xRebootRequestTicks) > pdMS_TO_TICKS(1500))
        {
            ESP_LOGI(TAG, "About to restart ...");
            esp_restart();
        }
    }
}

void MAIN_RequestReboot()
{
    m_xRebootRequestTicks = xTaskGetTickCount();
}


void MAIN_GetWiFiSTAIP(esp_netif_ip_info_t* pIPInfo)
{
    if (m_pWifiSTA != NULL)
        esp_netif_get_ip_info(m_pWifiSTA, pIPInfo);
}

int32_t MAIN_GetWiFiSTAIPv6(esp_ip6_addr_t if_ip6[CONFIG_LWIP_IPV6_NUM_ADDRESSES])
{
    if (m_pWifiSTA != NULL)
        return esp_netif_get_all_ip6(m_pWifiSTA, if_ip6);
    return 0;
}

void MAIN_GetWiFiSoftAPIP(esp_netif_ip_info_t* pIPInfo)
{
    if (m_pWifiSoftAP != NULL)
        esp_netif_get_ip_info(m_pWifiSoftAP, pIPInfo);
}

static void PrintCurrentTime()
{
    // Set timezone to Eastern Standard Time and print local time
    time_t now = 0;
    struct tm timeinfo = { 0 };
    setenv("TZ", "EST5EDT,M3.2.0/2,M11.1.0", 1);
    tzset();
    time(&now);
    localtime_r(&now, &timeinfo);
    ESP_LOGI(TAG, "The current date/time in New York is: %2d:%2d:%2d", (int)timeinfo.tm_hour, (int)timeinfo.tm_min, (int)timeinfo.tm_sec);
}

static void time_sync_notification_cb(struct timeval* tv)
{
    // settimeofday(tv, NULL);
    ESP_LOGI(TAG, "Notification of a time synchronization event, sec: %d", (int)tv->tv_sec);
    PrintCurrentTime();
}

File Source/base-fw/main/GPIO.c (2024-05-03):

#include "GPIO.h"
#include "FWConfig.h"
#include "Servo.h"
#include "Settings.h"
#include "driver/mcpwm.h"
#include "soc/mcpwm_periph.h"
#include "esp_log.h"
#include "driver/gpio.h"
#include "freertos/FreeRTOS.h"
#include "freertos/task.h"
#include "driver/rmt.h"
#include "led_strip.h"
#include "esp_log.h"
#include "driver/ledc.h"
#include "driver/uart.h"
#include <string.h>
#include "WhiteBox.h"
#include "HWConfig.h"
#include "driver/i2c.h"

#define TAG "GPIO"

static led_strip_handle_t led_strip;
static SSD1306_handle m_ssd1306;

void GPIO_Init()
{
    //install gpio isr service
    gpio_install_isr_service(0);

    // Sanity leds
    gpio_set_direction(HWCONFIG_WORMHOLELEDS_PIN, GPIO_MODE_OUTPUT);

    // Sanity leds
    gpio_set_direction(HWCONFIG_SANITY_PIN, GPIO_MODE_OUTPUT);

    // Ramp LEDs
    gpio_set_direction(HWCONFIG_RAMPLED_PIN, GPIO_MODE_OUTPUT);
    gpio_set_level(HWCONFIG_RAMPLED_PIN, false);

    // Stepper PINs
    gpio_set_direction(HWCONFIG_STEPPER_DIR_PIN, GPIO_MODE_OUTPUT);
    gpio_set_direction(HWCONFIG_STEPPER_STEP_PIN, GPIO_MODE_OUTPUT);
    gpio_set_direction(HWCONFIG_STEPPER_SLP_PIN, GPIO_MODE_OUTPUT);
    GPIO_StopStepper();

    // Servo PIN
    gpio_set_direction(HWCONFIG_SERVOMOTOR_PIN, GPIO_MODE_OUTPUT);
    // Initialize motor driver
    mcpwm_gpio_init(MCPWM_UNIT_1, MCPWM1A, HWCONFIG_SERVOMOTOR_PIN);
    mcpwm_config_t servo_config;
    servo_config.frequency = 50;  // Frequency = 50Hz,
    servo_config.cmpr_a = 0;      // Duty cycle of PWMxA = 0
    servo_config.cmpr_b = 0;      // Duty cycle of PWMxb = 0
    servo_config.counter_mode = MCPWM_UP_COUNTER;
    servo_config.duty_mode = MCPWM_DUTY_MODE_0;
    mcpwm_init(MCPWM_UNIT_1, MCPWM_TIMER_1, &servo_config);    // Configure PWM0A & PWM0B with above settings
    // 2/20 ms * 0.5*0.5
    GPIO_StopClamp(); // Don't piss off the servo motor


    // Init ramp LED
    // Prepare and then apply the LEDC PWM timer configuration
    ledc_timer_config_t ledc_timer = {
        .speed_mode       = LEDC_LOW_SPEED_MODE,
        .timer_num        = LEDC_TIMER_0,
        .duty_resolution  = LEDC_TIMER_12_BIT,
        .freq_hz          = 5000,  // Set output frequency at 5 kHz
        .clk_cfg          = LEDC_AUTO_CLK
    };
    ESP_ERROR_CHECK(ledc_timer_config(&ledc_timer));

    // Prepare and then apply the LEDC PWM channel configuration
    ledc_channel_config_t ledc_channel = {
        .speed_mode     = LEDC_LOW_SPEED_MODE,
        .channel        = LEDC_CHANNEL_0,
        .timer_sel      = LEDC_TIMER_0,
        .intr_type      = LEDC_INTR_DISABLE,
        .gpio_num       = HWCONFIG_RAMPLED_PIN,
        .duty           = 0, // Set duty to 0%
        .hpoint         = 0
    };
    ESP_ERROR_CHECK(ledc_channel_config(&ledc_channel));
    GPIO_SetRampLightPerc(false);

    // Initialize GPIO for home sensor
    gpio_set_direction(HWCONFIG_HOMESENSOR_PIN, GPIO_MODE_INPUT);
    gpio_pullup_en(HWCONFIG_HOMESENSOR_PIN);

    /* LED strip initialization with the GPIO and pixels number*/
    led_strip_config_t strip_config = {
        .strip_gpio_num = HWCONFIG_WORMHOLELEDS_PIN,
        .max_leds = HWCONFIG_WORMHOLELEDS_LEDCOUNT, // sanity LED + at least one LED on board
    };
    led_strip_rmt_config_t rmt_config = {
        .resolution_hz = 10 * 1000 * 1000, // 10MHz
    };
    ESP_ERROR_CHECK(led_strip_new_rmt_device(&strip_config, &rmt_config, &led_strip));
    /* Set all LED off to clear all pixels */
    led_strip_clear(led_strip);

    #ifndef WHITEBOX_SOUNDFX_DEACTIVATE
    // =====================
    // UART drive to drive the Mp3 player
        /* Configure parameters of an UART driver,
     * communication pins and install the driver */
    uart_config_t uart_config = {
        .baud_rate = HWCONFIG_MP3PLAYER_BAUDRATE,
        .data_bits = UART_DATA_8_BITS,
        .parity    = UART_PARITY_DISABLE,
        .stop_bits = UART_STOP_BITS_1,
        .flow_ctrl = UART_HW_FLOWCTRL_DISABLE,
        .source_clk = UART_SCLK_APB,
    };
    int intr_alloc_flags = 0;
    #if CONFIG_UART_ISR_IN_IRAM
        intr_alloc_flags = ESP_INTR_FLAG_IRAM;
    #endif

    ESP_ERROR_CHECK(uart_driver_install(HWCONFIG_MP3PLAYER_PORT_NUM, HWCONFIG_MP3PLAYER_BUFFSIZE * 2, 0, 0, NULL, intr_alloc_flags));
    ESP_ERROR_CHECK(uart_param_config(HWCONFIG_MP3PLAYER_PORT_NUM, &uart_config));
    ESP_ERROR_CHECK(uart_set_pin(HWCONFIG_MP3PLAYER_PORT_NUM, HWCONFIG_MP3PLAYER_TX2RXD, HWCONFIG_MP3PLAYER_RX2TXD, -1, -1));
    #endif

	const int i2c_master_port = HWCONFIG_I2C_MASTER_NUM;
    i2c_config_t conf = {0};
    conf.mode = I2C_MODE_MASTER;
    conf.sda_io_num = HWCONFIG_I2C_SDA;
    conf.sda_pullup_en = GPIO_PULLUP_ENABLE;
    conf.scl_io_num = HWCONFIG_I2C_SCL;
    conf.scl_pullup_en = GPIO_PULLUP_ENABLE;
    conf.master.clk_speed = HWCONFIG_I2C_MASTER_FREQ_HZ;
    i2c_param_config(i2c_master_port, &conf);

	ESP_ERROR_CHECK(i2c_driver_install(i2c_master_port, conf.mode, HWCONFIG_I2C_MASTER_RX_BUF_DISABLE, HWCONFIG_I2C_MASTER_TX_BUF_DISABLE, 0));
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

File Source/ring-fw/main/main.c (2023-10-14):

/*  WiFi softAP Example

   This example code is in the Public Domain (or CC0 licensed, at your option.)

   Unless required by applicable law or agreed to in writing, this
   software is distributed on an "AS IS" BASIS, WITHOUT WARRANTIES OR
   CONDITIONS OF ANY KIND, either express or implied.
*/
#include "FWConfig.h"
#include "HelperMacro.h"
#include <string.h>
#include "freertos/FreeRTOS.h"
#include "freertos/task.h"
#include "esp_system.h"
#include "esp_event.h"
#include "esp_log.h"
#include "nvs_flash.h"
#include "esp_pm.h"
#include "sdkconfig.h"
#include "lwip/err.h"
#include "lwip/sys.h"
#include "lwip/ip4_addr.h"
#include "esp_system.h"
#include "driver/gpio.h"
#include "gpio.h"
#include "SGUBRProtocol.h"
#include "SGUBRComm.h"
#include "SGUHelper.h"
#include "esp_now.h"
#include "esp_crc.h"
#include "esp_netif.h"
#include "esp_wifi.h"
#include "esp_ota_ops.h"

#define SGU_GATTS_TAG "SGU-GATTS"

#define LED_OUTPUT_MAX (160)
#define LED_OUTPUT_IDLE (100)

static void InitESPNOW();

static const char *TAG = "Main";

const uint8_t m_u8BroadcastAddress[] = {0xFF, 0xFF, 0xFF, 0xFF, 0xFF, 0xFF};

static volatile bool m_bIsSuicide = false;
static volatile TickType_t m_lAutoOffTicks = 0;
static volatile TickType_t m_ulAutoOffTimeoutMs = FWCONFIG_HOLDPOWER_DELAY_MS;

// Chevron animation
static volatile int32_t m_s32ChevronAnim = -1;

static esp_pm_lock_handle_t m_lockHandle;

void app_main();
static void ResetAutoOffTicks();

static void SGUBRKeepAliveHandler(const SGUBRPROTOCOL_SKeepAliveArg* psKeepAlive);
static void SGUBRTurnOffHandler();
static void SGUBRUpdateLightHandler(const SGUBRPROTOCOL_SUpdateLightArg* psArg);
static void SGUBRChevronsLightningHandler(const SGUBRPROTOCOL_SChevronsLightningArg* psChevronLightningArg);
static void SGUBRGotoFactory();

static const SGUBRPROTOCOL_SConfig m_sConfig =
{
    .fnKeepAliveHandler = SGUBRKeepAliveHandler,
    .fnTurnOffHandler = SGUBRTurnOffHandler,
    .fnUpdateLightHandler = SGUBRUpdateLightHandler,
    .fnChevronsLightningHandler = SGUBRChevronsLightningHandler,
    .fnGotoFactoryHandler = SGUBRGotoFactory,
    .fnGotoOTAModeHandler = NULL
};

static SGUBRCOMM_SHandle m_sSGUBRCommHandle;
static SGUBRCOMM_SSetting m_sSetting = { .eMode = SGUBRCOMM_EMODE_Ring, .psSGUBRProtocolConfig = &m_sConfig };

static void wifi_event_handler(void* arg, esp_event_base_t event_base, int32_t event_id, void* event_data);
static void wifistation_event_handler(void* arg, esp_event_base_t event_base, int32_t event_id, void* event_data);

static void InitESPNOW()
{
    wifi_init_config_t cfg = WIFI_INIT_CONFIG_DEFAULT();
    ESP_ERROR_CHECK(esp_wifi_init(&cfg));

    ESP_ERROR_CHECK(esp_wifi_set_mode(WIFI_MODE_STA) );

    // Soft Access Point Mode
    esp_netif_t* wifiSTA = esp_netif_create_default_wifi_sta();

    esp_netif_ip_info_t ipInfoSTA;
    IP4_ADDR(&ipInfoSTA.ip, 192, 168, 66, 250);
	IP4_ADDR(&ipInfoSTA.gw, 192, 168, 66, 250);
	IP4_ADDR(&ipInfoSTA.netmask, 255, 255, 255, 0);
    esp_netif_dhcpc_stop(wifiSTA);
	esp_netif_set_ip_info(wifiSTA, &ipInfoSTA);

    esp_event_handler_instance_t instance_any_id;
    esp_event_handler_instance_t instance_got_ip;
    ESP_ERROR_CHECK(esp_event_handler_instance_register(WIFI_EVENT,
                                                        ESP_EVENT_ANY_ID,
                                                        &wifistation_event_handler,
                                                        NULL,
                                                        &instance_any_id));
    ESP_ERROR_CHECK(esp_event_handler_instance_register(IP_EVENT,
                                                        IP_EVENT_STA_GOT_IP,
                                                        &wifistation_event_handler,
                                                        NULL,
                                                        &instance_got_ip));

    wifi_config_t wifi_configSTA = {
        .sta = {
            /* Setting a password implies station will connect to all security modes including WEP/WPA.
             * However these modes are deprecated and not advisable to be used. Incase your Access point
             * doesn't support WPA2, these mode can be enabled by commenting below line */
            .pmf_cfg = {
                .capable = true,
                .required = false
            },
        },
    };
    strcpy((char*)wifi_configSTA.sta.ssid, FWCONFIG_MASTERBASE_SSID);

    if (strlen(FWCONFIG_MASTERBASE_PASS) == 0)
    {
        wifi_configSTA.sta.threshold.authmode = WIFI_AUTH_OPEN;
    }
    else
    {
        wifi_configSTA.sta.threshold.authmode = WIFI_AUTH_WPA2_PSK;
        strcpy((char*)wifi_configSTA.sta.password, FWCONFIG_MASTERBASE_PASS);
    }

    ESP_ERROR_CHECK(esp_wifi_set_config(WIFI_IF_STA, &wifi_configSTA) );

    // Start AP + STA
    ESP_ERROR_CHECK(esp_wifi_start() );
}
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

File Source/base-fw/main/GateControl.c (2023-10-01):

#include <stdint.h>
#include <string.h>
#include <math.h>
#include "HelperMacro.h"
#include "GateControl.h"
#include "freertos/FreeRTOS.h"
#include "freertos/task.h"
#include "freertos/semphr.h"
#include "esp_attr.h"
#include "esp_log.h"
#include "FWConfig.h"
#include "GPIO.h"
#include "Settings.h"
#include "driver/gpio.h"
#include "SGUBRComm.h"
#include "SGUBRProtocol.h"
#include "SGUHelper.h"
#include "Main.h"
#include "ClockMode.h"
#include "GateControl.h"
#include "GateStepper.h"
#include "SoundFX.h"

#define TAG "GateControl"

typedef struct
{
    void (*OnError)(const char* szError);
} SProcCycle;

// Private variables
static volatile GATECONTROL_EMODE m_eNextMode = GATECONTROL_EMODE_Idle;
static volatile GATECONTROL_UModeArg m_uNextModeArgument;

// Current working variables ...
static GATECONTROL_EMODE m_eCurrentMode;
static GATECONTROL_UModeArg m_uCurrentModeArg;
static bool m_bhasCurrentLastError = false;
static char m_szCurrentLastError[128+1] = { 0, };

static volatile bool m_bIsStop = false;

// Control homing and encoder.
static StaticSemaphore_t m_xSemaphoreCreateMutex;
static SemaphoreHandle_t m_xSemaphoreHandle;

static TaskHandle_t m_sGateControlHandle;

static int32_t m_s32Count = 0;

static bool m_bIsHomingCompleted = false;

static void GateControlTask( void *pvParameters );

static void MoveTo(int32_t* ps32Count, int32_t s32Target);
static void MoveRelative(int32_t s32RelativeTarget);
static bool MoveUntilHomeSwitch(bool bHomeSwitchState, uint32_t u32TimeOutMS, int32_t* ps32Count);

static int32_t GetAbsoluteSymbolTarget(uint8_t u8SymbolIndex, int32_t s32StepPerRotation);

static bool AutoCalibrate(const SProcCycle* psProcCycle);
static bool DoHoming(const SProcCycle* psProcCycle);
static bool DoDialSequence(const GATECONTROL_SDialArg* psDialArg, const SProcCycle* psProcCycle);

static void ProcCycleError(const char* szError);

void GATECONTROL_Init()
{
    m_xSemaphoreHandle = xSemaphoreCreateMutexStatic(&m_xSemaphoreCreateMutex);
    configASSERT( m_xSemaphoreHandle );
}

void GATECONTROL_Start()
{
	if (xTaskCreatePinnedToCore(GateControlTask, "gatecontrol", FWCONFIG_GATECONTROL_STACKSIZE, (void*)NULL, FWCONFIG_GATECONTROL_PRIORITY_DEFAULT, &m_sGateControlHandle, FWCONFIG_GATECONTROL_COREID) != pdPASS )
	{
		ESP_ERROR_CHECK(ESP_FAIL);
	}
}

static void GateControlTask( void *pvParameters )
{
    ESP_LOGI(TAG, "GateControl task started");

    GATECONTROL_DoAction(GATECONTROL_EMODE_GoHome, NULL);
    // GATECONTROL_AnimRampLight(true);

	while(1)
	{
        // Clear the wormhole
        WORMHOLE_FullStop();

        xSemaphoreTake(m_xSemaphoreHandle, portMAX_DELAY);

        // Start new process ....
        m_eCurrentMode = m_eNextMode;
        m_uCurrentModeArg = m_uNextModeArgument;

        // Reset temporary vars ...
        m_eNextMode = GATECONTROL_EMODE_Idle;
        memset((void*)&m_uNextModeArgument, 0, sizeof(GATECONTROL_UModeArg));
        m_bIsStop = false;

        xSemaphoreGive(m_xSemaphoreHandle);

        if (m_eCurrentMode == GATECONTROL_EMODE_Idle)
        {
            vTaskDelay(pdMS_TO_TICKS(100));
            continue;
        }

        // Reset last error latch
        xSemaphoreTake(m_xSemaphoreHandle, portMAX_DELAY);
        m_bhasCurrentLastError = false;
        m_szCurrentLastError[0] = 0;
        xSemaphoreGive(m_xSemaphoreHandle);

        SProcCycle sProcCycle = { .OnError = ProcCycleError };

        if (m_eCurrentMode == GATECONTROL_EMODE_GoHome)
        {
            SGUBRCOMM_ChevronLightning(&g_sSGUBRCOMMHandle, SGUBRPROTOCOL_ECHEVRONANIM_FadeIn);
            vTaskDelay(pdMS_TO_TICKS(750));
            if (DoHoming(&sProcCycle))
                SGUBRCOMM_ChevronLightning(&g_sSGUBRCOMMHandle, SGUBRPROTOCOL_ECHEVRONANIM_FadeOut);
            else
                SGUBRCOMM_ChevronLightning(&g_sSGUBRCOMMHandle, SGUBRPROTOCOL_ECHEVRONANIM_ErrorToOff);
        }
        else if (m_eCurrentMode == GATECONTROL_EMODE_AutoCalibrate)
        {
            if (AutoCalibrate(&sProcCycle))
            {
                DoHoming(&sProcCycle);
            }
        }
        else if (m_eCurrentMode == GATECONTROL_EMODE_Dial)
        {
            if (DoDialSequence(&m_uCurrentModeArg.sDialArg, &sProcCycle))
            {
                // Go back to home ...
                vTaskDelay(pdMS_TO_TICKS(5000));

                // We give a chance to home ...
                m_bIsStop = false;
                DoHoming(&sProcCycle);
            }
        }
        else if (m_eCurrentMode == GATECONTROL_EMODE_ActiveClock)
        {
            ESP_LOGI(TAG, "GateControl activate clock mode");
            CLOCKMODE_Run(&m_bIsStop);
        }
        else if (m_eCurrentMode == GATECONTROL_EMODE_ManualReleaseClamp)
        {
            ESP_LOGI(TAG, "GateControl release clamp");
            GPIO_ReleaseClamp();
            vTaskDelay(pdMS_TO_TICKS(5));
        }
        else if (m_eCurrentMode == GATECONTROL_EMODE_ManualLockClamp)
        {
            ESP_LOGI(TAG, "GateControl lock clamp");
            GPIO_LockClamp();
            vTaskDelay(pdMS_TO_TICKS(5));
        }
        else if (m_eCurrentMode == GATECONTROL_EMODE_ManualWormhole)
        {
            ESP_LOGI(TAG, "GateControl manual wormhole");
            const WORMHOLE_SArg sArg = { .eType = m_uCurrentModeArg.sManualWormhole.eWormholeType, .bNoTimeLimit = true };
            WORMHOLE_Open(&sArg, &m_bIsStop);
            WORMHOLE_Run(&m_bIsStop);
            WORMHOLE_Close(&m_bIsStop);
        }

        vTaskDelay(pdMS_TO_TICKS(1));
	}
	vTaskDelete( NULL );
}

static int32_t GetAbsoluteSymbolTarget(uint8_t u8SymbolIndex, int32_t s32StepPerRotation)
{
    const uint32_t u32SymbolLedIndex = SGUHELPER_SymbolIndexToLedIndex(u8SymbolIndex);
    const double dblPercent = (SGUHELPER_LEDIndexToDeg(u32SymbolLedIndex) / 360.0d);
    return dblPercent * (double)s32StepPerRotation * -1;
}
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

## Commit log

2023-03-05 Feature/maxou/switch led lib (#61)
    * disconnection display
    * move button
    * remove useless call
    * new factory program library with webserver
    * reactivate sound
    * remove fast-led and switch to C only
    * fix file case
    * fwconfig
    * fix case
    [partitions.csv]
2023-03-05 Doc/maxou/update doc img+autocalib (#62)
    * auto calibration button
    * ring back components
2023-03-18 Feature/maxou/ring comm (#63)
    * Change sequence to wakeup the gate
    * more time to release the clamp
    * Ring control
    * remove useless stuffs
2023-04-05 Feature/maxou/update board pcb (#66)
    * update pcb, separate hardware config from firmware
    * remove warnings mostly and rearrange files
    * move function and do some clean-up
    * Move API code
    * rename main file
    * update image
    * SGU base PCB update
    * fix pcb error + code
    * fix compilation
    ---------
    [FWConfig.h, GPIO.c, GateControl.c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]
2023-04-05 Chore/maxou/doc pcb update (#67)
    * doc PCB
    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
2023-04-16 Feature/maxou/oled screen (#68)
    * OLED
    * display IP information on OLED
    * update SSID name
    * more board image
    * typo
    [Board-holder_4mm-x1.stl]
2023-05-06 Feature/maxou/update idf 5 (#69)
    * Fix
    * remove make list
    * makelist
    * fix idf5
    * almost compile
    * ring-fw compile ... but not tested
    * factory compile
    * base-fw
    * update docker
    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
    [FWConfig.h, GPIO.c, GateControl.c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]
2023-09-17 Feature/maxou/wormhole experiment (#71)
    * attempt to fix wifi
    * small test .. + idf 5.1
    * blackhole effect
    * Wormhole address
    * hell mode
    * move fluid movements
    * lower speed
    [GPIO.c, GateStepper.c, Main.c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]
2023-09-17 Feature/maxou/ax b formula stepper (#72)
    * SG1-gate
    * make "infinite" gear
    * test speed
    * Change speed values
    * use idf 5.1
2023-09-25 Feature/maxou/all symbol light up (#73)
    * ring at idf 5.1.0
    * reduce symbol illumination when all is lit
    * new glitch effect
    * lower maximum for blackhole
    * increase maximum for normal wormhole
    * Glitch effect
    * update partitions
    * remove useless file
    [partitions.csv]
2023-09-25 Feature/maxou/update led strip (#74)
    * Replace LED_Strip component
    * add led strip using the package manager
    [FWConfig.h, GPIO.c, fwconfig.h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]
2023-09-30 Feature/maxou/adjust brigness log (#75)
    * Logarithmic adjustement to ramp lightning
    * Linear lightning animation on the ring
    * Lowered power consumption
    * fix bug where red lightning doesn't go at 0
    [GateControl.c, Wormhole.c, main.c]
2023-10-03 Doc/maxou/update doc (#77)
    * fix settings
    * Fix mistakes
    * fix more stuff ...
    * fix stuff again
    [Settings.c]
2023-10-07 Feature/maxou/ipv6 test (#78)
    * remove ipv6
    * deactivate ipv6
    * activate again ... but doesn't work yet
    * request an IPv6
    * Add IPv6 addresses and fix the bug making the mp3 player play randomly
    * remove useless
    * fix helper macros
    [GateStepper.c, Main.c, SoundFX.c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]
2023-10-14 Feature/maxou/ring report poweroff (#79)
    * red color for shutdown position mode
2023-10-25 Gerber file (#81)
